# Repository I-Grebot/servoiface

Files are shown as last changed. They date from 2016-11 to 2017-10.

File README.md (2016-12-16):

# servoiface

DC Servo motor interface

Board use to control a DC motor and act as a servomotor, based on STM32F042 MCU. 

Position feedback can be provided by potentiometer, limit switches or encoder. 

Reference position command can be provided from a PWM signal such as regular RC servomotors, or an halfduplex UART such as Dynamixel smart servomotors.

Motor current limitation can be driven, thus the device can be used as a torque controlled system (useful for robot gripper, for instance).

Debug RGB, tactile switch, and potentiometer can be used for system calibration and visual feedback.

Board:

board

Schematics:

sch

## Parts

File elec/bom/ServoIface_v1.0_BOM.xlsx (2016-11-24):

Cmd | Qty | Value | Device | Package | Parts | Description
 | 3 |  | JUMPER-3SMD | SJ_3 | J_ES1, J_ES2, J_REF
 | 1 |  | JUMPER-PAD-2-NO | PAD-JUMPER-2-NO_NO_SILK | J_CMD
 | 1 |  | LNRG_4026 | NRG_4026 | L1
 | 2 |  | M03SCREW | SCREWTERMINAL-3.5MM-3 | POT, VIN1 | Header 3
 | 2 |  | M04SCREW | SCREWTERMINAL-3.5MM-4 | ENCODER, ENDSTOPS | Header 4
 | 5 |  | R0603 | R0603 | R3, R5, R7, R8, R9
 | 2 |  | SWITCH-MOMENTARY-2SMD-3 | TACTILE_SWITCH_SMD-3 | S1, S_RST | Various NO switches- pushbuttons, reed, etc
 | 1 | 47UF | C_PANAFM1E470-P2.0 | CAPPR200-500X1600 | C13 | Aluminum Electrolytic Capacitors
 | 1 | 0.15 | R2512 | CRF2512 | R1
 | 3 | 100nF | C0603 | R0603 | C1, C6, C10
 | 1 | 105k | R0603 | R0603 | R11
 | 1 | 10nF | C0603 | R0603 | C2
 | 2 | 10uF | C0805 | R0805 | C7, C8
 | 1 | 10uF | C1206 | 1206 | C9
 | 2 | 1uF | C0805 | R0805 | C3, C11
 | 1 | 2.2uF | C0805 | R0805 | C12
 | 1 | 20k | R0603 | R0603 | R12
 | 1 | 330k | R0603 | R0603 | R6
 | 3 | 4.7k | R0603 | R0603 | R2, R4, R10
 | 1 | 4.7uF | C0805 | R0805 | C4
 | 1 | 470nF | C0603 | R0603 | C5
 | 1 | DRV8870 | DRV8870 | HSOP_8P | IC4 | DRV8870 3.6-A Brushed DC Motor Driver (PWM Control)
 | 1 | HEAT_SINK | HEAT_SINK | HEAT_A5_SA | H1 | ICK SMD A 5 SA Farnell 4302163
 | 1 | J_SWD | ZIF-06-1MM | ZIF-06-1MM | J1
 | 1 | LED-TRICOLOR | LED-TRICOLOR | PLCC4 | RGB | Tri-Color LED SMD
 | 1 | LP2980 | LP2980 | SOT23-5L | IC3
 | 1 | M023.5MM | M023.5MM | SCREWTERMINAL-3.5MM-2 | MOTOR | Standard 2-pin 0.1 header. Use with"
 | 2 | NC | R0603 | R0603 | R13, R14
 | 1 | STM32F042 | STM32F042 | TSSOP20 | IC1 | ARM®-based 32-bit MCU, up to 32 KB Flash, crystal-less USB
 | 3 | TEST_POINT_R04 | TEST_POINT_R04 | TP_R04 | TP1, TP2, TP3
Ti | 1 | TPS560200 | TPS560200 | SOT23-5L | IC2
 | 1 | TRIMPOTCB10 | TRIMPOTCB10 | POT_CB10 | P1 | Various small potentiometers for set-and-forget" applications"

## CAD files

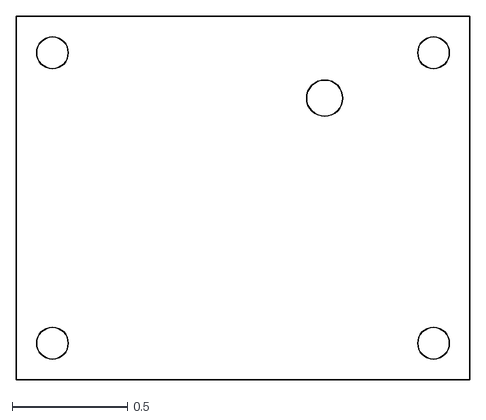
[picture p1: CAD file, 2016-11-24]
elec/dxf/ServoIface_v1.0.dxf
1.97 x 1.57

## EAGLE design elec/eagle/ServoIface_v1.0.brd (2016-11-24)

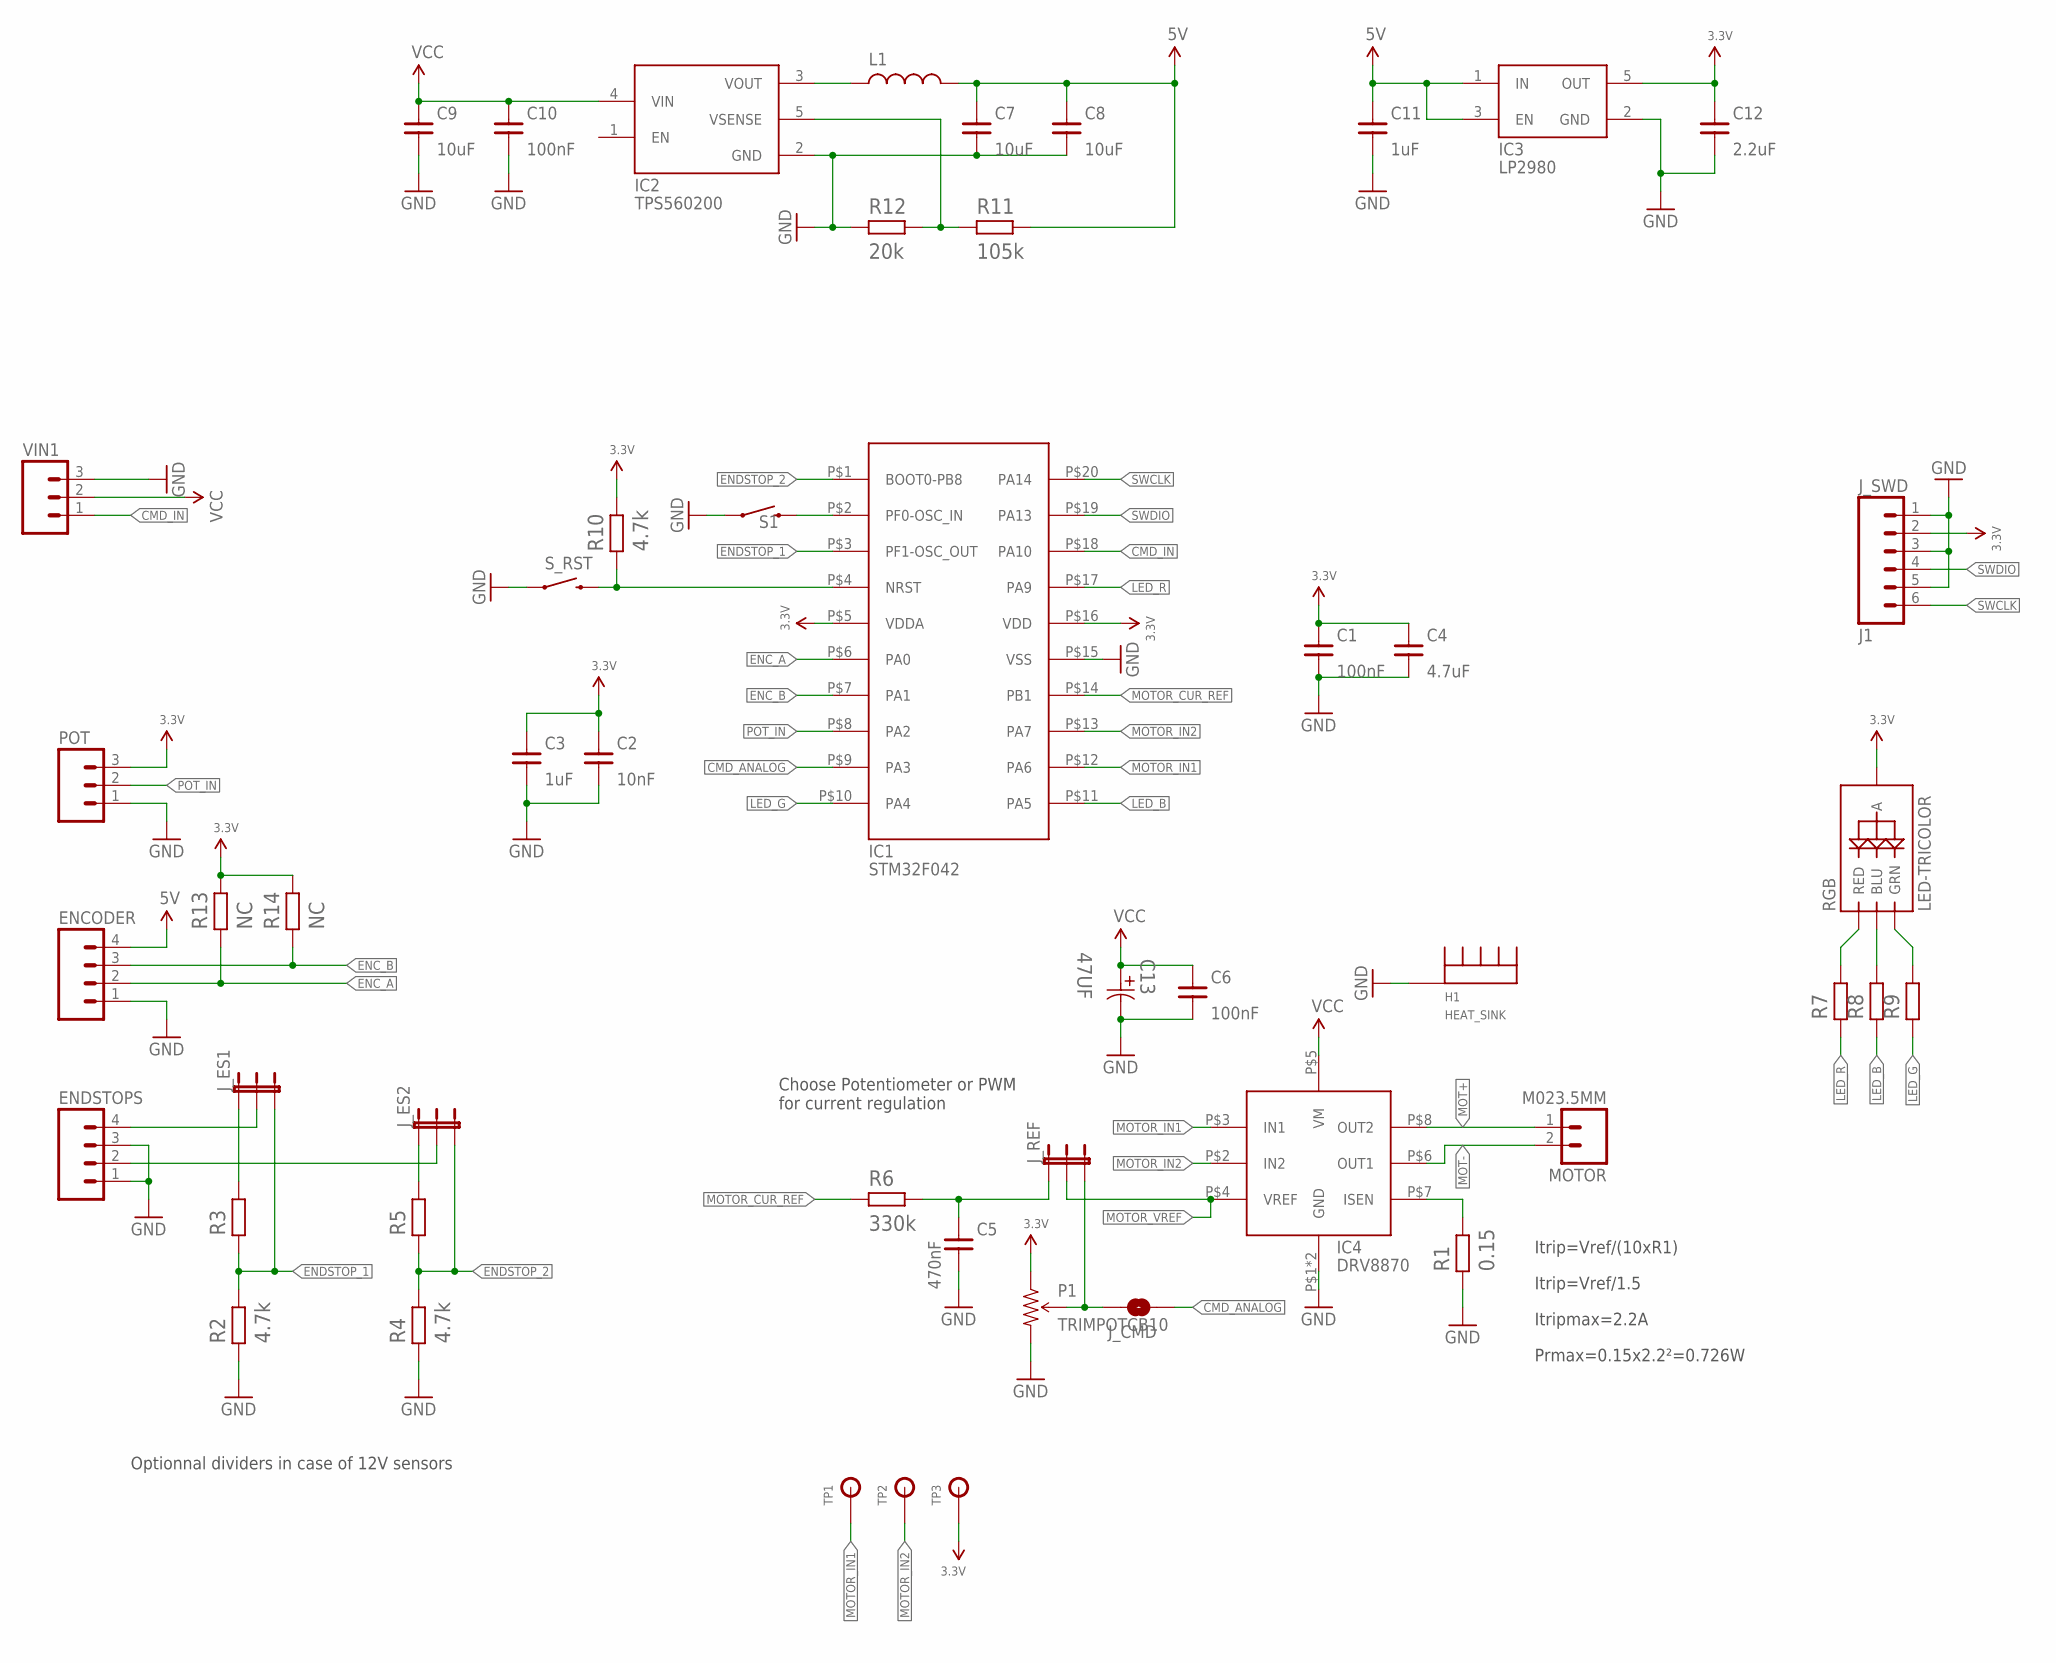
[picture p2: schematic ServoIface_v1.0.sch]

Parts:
C1, C6, C10: 100nF; R0603
C2: 10nF; R0603
C3, C11: 1uF; R0805
C4: 4.7uF; R0805
C5: 470nF; R0603
C7, C8: 10uF; R0805
C9: 10uF; 1206
C12: 2.2uF; R0805
C13: 47UF; CAPPR200-500X1600
ENCODER: M04SCREW; SCREWTERMINAL-3.5MM-4
ENDSTOPS: M04SCREW; SCREWTERMINAL-3.5MM-4
H1: HEAT_SINK; HEAT_A5_SA
IC1: STM32F042; TSSOP20
IC2: TPS560200; SOT23-5L
IC3: LP2980; SOT23-5L
IC4: DRV8870; HSOP_8P
J1: J_SWD; ZIF-06-1MM
J_CMD: JUMPER-PAD-2-NO; PAD-JUMPER-2-NO_NO_SILK
J_ES1, J_ES2: JUMPER-3SMD; SJ_3
J_REF: JUMPER-3SMD; SJ_3
L1: LNRG_4026; NRG_4026
MOTOR: M023.5MM; SCREWTERMINAL-3.5MM-2
P1: TRIMPOTCB10; POT_CB10
POT: M03SCREW; SCREWTERMINAL-3.5MM-3
R1: 0.15; CRF2512
R2, R4, R10: 4.7k; R0603
R3, R5, R7, R8, R9: R0603
R6: 330k; R0603
R11: 105k; R0603
R12: 20k; R0603
R13, R14: NC; R0603
RGB: LED-TRICOLOR; PLCC4
S1: SWITCH-MOMENTARY-2SMD-3; TACTILE_SWITCH_SMD-3
S_RST: SWITCH-MOMENTARY-2SMD-3; TACTILE_SWITCH_SMD-3
TP1, TP2, TP3: TEST_POINT_R04; TP_R04
VIN1: M03SCREW; SCREWTERMINAL-3.5MM-3

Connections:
3.3V: C1.2, C2.2, C3.2, C4.2, C12.2, IC1.P$5 (VDDA), IC1.P$16 (VDD), IC3.5 (OUT), J1.2, P1.P$1 (CCW), POT.3, R10.2, R13.2, R14.2, RGB.P$1 (A), TP3.P$1
5V: C7.2, C8.2, C11.2, ENCODER.4, IC3.1 (IN), IC3.3 (EN), L1.P$2 (2), R11.2
CMD_ANALOG: IC1.P$9 (PA3), J_CMD.1
CMD_IN: IC1.P$18 (PA10), VIN1.1
ENC_A: ENCODER.2, IC1.P$6 (PA0), R13.1
ENC_B: ENCODER.3, IC1.P$7 (PA1), R14.1
ENDSTOP_1: IC1.P$3 (PF1-OSC_OUT), J_ES1.3, R2.2, R3.1
ENDSTOP_2: IC1.P$1 (BOOT0-PB8), J_ES2.3, R4.2, R5.1
GND: C1.1, C2.1, C3.1, C4.1, C5.1, C6.1, C7.1, C8.1, C9.1, C10.1, C11.1, C12.1, C13.2, ENCODER.1, ENDSTOPS.1, ENDSTOPS.3, H1.P$1, IC1.P$15 (VSS), IC2.2 (GND), IC3.2 (GND), IC4.P$1 (GND), IC4.PAD (GND), J1.1, J1.3, J1.5, P1.P$2 (CW), POT.1, R1.P$1 (1), R2.1, R4.1, R12.1, S1.1, S_RST.1, VIN1.3
LED_B: IC1.P$11 (PA5), R8.1
LED_G: IC1.P$10 (PA4), R9.1
LED_R: IC1.P$17 (PA9), R7.1
MOT+: IC4.P$8 (OUT2), MOTOR.1
MOT-: IC4.P$6 (OUT1), MOTOR.2
MOTOR_CUR_REF: IC1.P$14 (PB1), R6.1
MOTOR_IN1: IC1.P$12 (PA6), IC4.P$3 (IN1), TP1.P$1
MOTOR_IN2: IC1.P$13 (PA7), IC4.P$2 (IN2), TP2.P$1
MOTOR_VREF: IC4.P$4 (VREF), J_REF.2
unnamed: IC4.P$7 (ISEN), R1.P$2 (2)
unnamed: ENDSTOPS.2, J_ES2.2
unnamed: J_ES2.1, R5.2
unnamed: ENDSTOPS.4, J_ES1.2
unnamed: J_ES1.1, R3.2
unnamed: J_CMD.2, J_REF.3, P1.P$3 (WIPER)
unnamed: C5.2, J_REF.1, R6.2
unnamed: R7.2, RGB.P$4 (RED)
unnamed: R8.2, RGB.P$2 (BLU)
unnamed: R9.2, RGB.P$3 (GRN)
unnamed: IC1.P$4 (NRST), R10.1, S_RST.4 (2)
unnamed: IC2.3 (VOUT), L1.P$1 (1)
unnamed: IC2.5 (VSENSE), R11.1, R12.2
POT_IN: IC1.P$8 (PA2), POT.2
SW1: IC1.P$2 (PF0-OSC_IN), S1.4 (2)
SWCLK: IC1.P$20 (PA14), J1.6
SWDIO: IC1.P$19 (PA13), J1.4
VCC: C6.2, C9.2, C10.2, C13.1, IC2.4 (VIN), IC4.P$5 (VM), VIN1.2

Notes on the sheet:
Itrip=Vref/(10xR1)
Itrip=Vref/1.5
Itripmax=2.2A
Optionnal dividers in case of 12V sensors
Choose Potentiometer or PWM for current regulation
Prmax=0.15x2.2²=0.726W

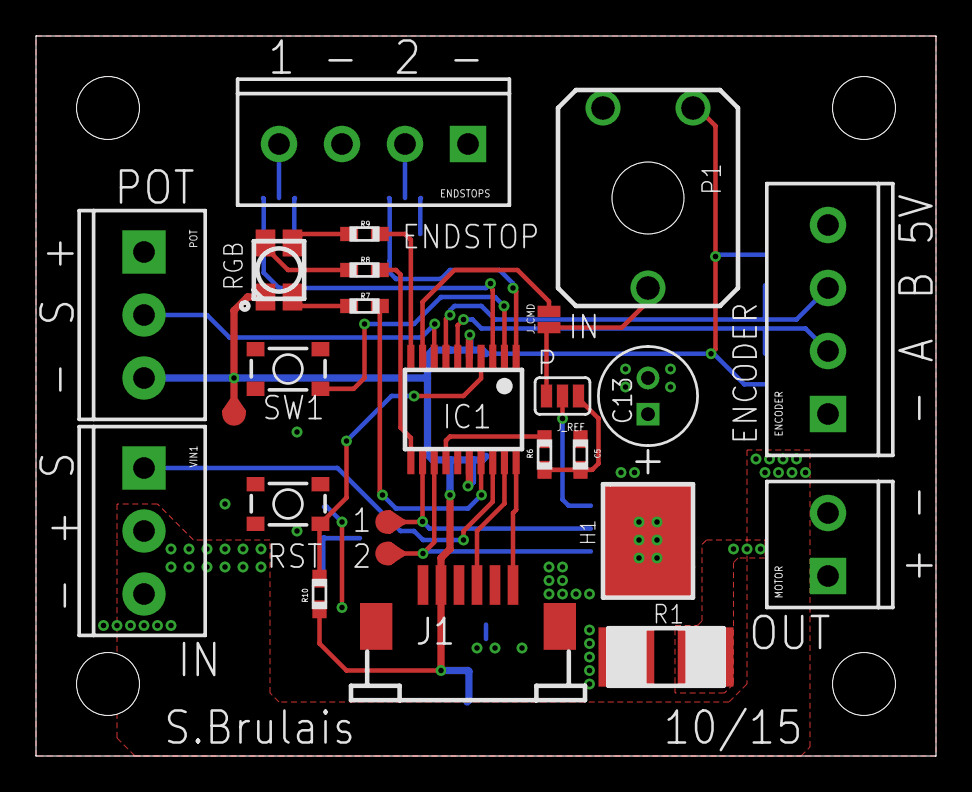
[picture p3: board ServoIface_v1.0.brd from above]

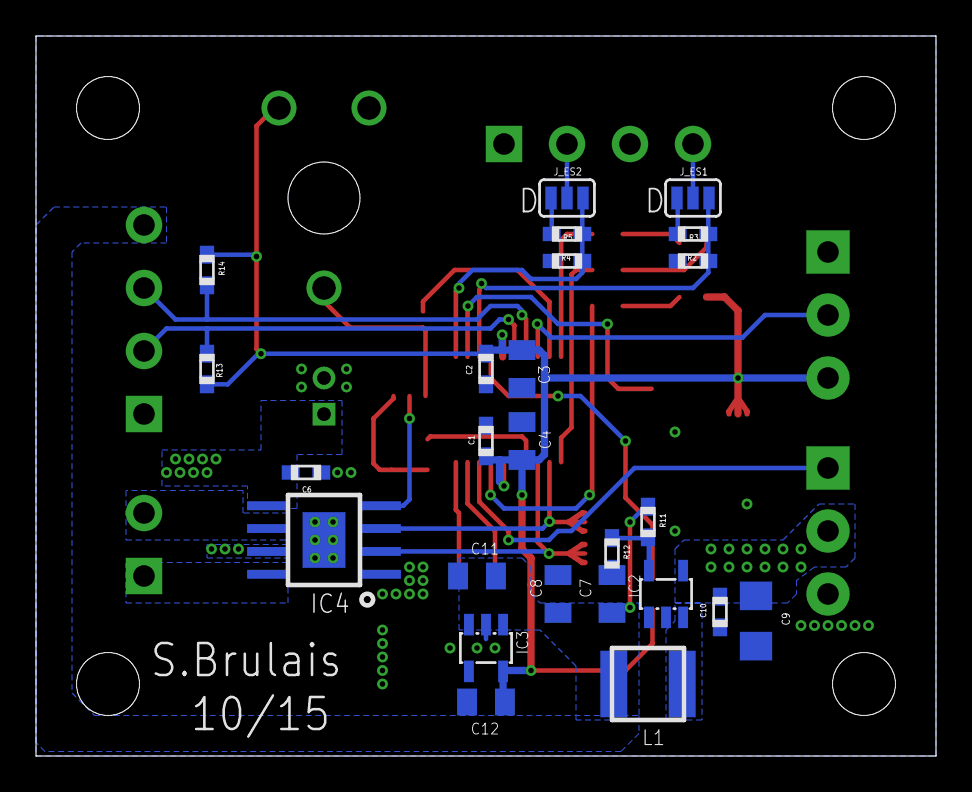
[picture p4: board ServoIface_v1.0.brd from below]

Board: 2 copper layers, 50.0 x 40.0 mm, 50 parts (25 on the bottom side), 36 nets.

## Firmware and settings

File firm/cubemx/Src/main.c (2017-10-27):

/**
  ******************************************************************************
  * File Name          : main.c
  * Description        : Main program body
  ******************************************************************************
  *
  * Copyright (c) 2017 STMicroelectronics International N.V. 
  * All rights reserved.
  *
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
  ******************************************************************************
  */
/* Includes ------------------------------------------------------------------*/
#include "main.h"
#include "stm32f0xx_hal.h"
#include "cmsis_os.h"



/* USER CODE BEGIN Includes */
#include "ServoIface.h"
#include "pid.h"

/* USER CODE END Includes */

ADC_HandleTypeDef hadc;
DMA_HandleTypeDef hdma_adc;

TIM_HandleTypeDef htim1;
TIM_HandleTypeDef htim2;
TIM_HandleTypeDef htim3;

osThreadId MotorCtrlTaskIdHandle;
osThreadId RGBLedTaskIdHandle;
osThreadId AutoTestTaskIdHandle;
osSemaphoreId selfTestSemHandle;

/* USER CODE BEGIN PV */
PID_process_t *pPID;
volatile uint32_t pwm=0;


/* USER CODE END PV */

void SystemClock_Config(void);
void Error_Handler(void);
static void MX_GPIO_Init(void);
static void MX_DMA_Init(void);
static void MX_ADC_Init(void);
static void MX_TIM1_Init(void);
static void MX_TIM2_Init(void);
static void MX_TIM3_Init(void);
void MotorCtrlTask(void const * argument);
void RGBLedTask(void const * argument);
void PIDTask(void const * argument);

void HAL_TIM_MspPostInit(TIM_HandleTypeDef *htim);
                                

/* USER CODE BEGIN PFP */

/* USER CODE END PFP */

int main(void)
{

  /* MCU Configuration----------------------------------------------------------*/

  /* Reset of all peripherals, Initializes the Flash interface and the Systick. */
  HAL_Init();

  /* Configure the system clock */
  SystemClock_Config();

  /* Initialize all configured peripherals */
  MX_GPIO_Init();
  MX_DMA_Init();
  MX_ADC_Init();
  MX_TIM1_Init();
  MX_TIM2_Init();
  MX_TIM3_Init();

  /* USER CODE BEGIN 2 */


  HAL_TIM_PWM_Start(&htim3, TIM_CHANNEL_1);
  HAL_TIM_PWM_Start(&htim3, TIM_CHANNEL_2);
  HAL_TIM_Encoder_Start(&htim2,TIM_CHANNEL_1|TIM_CHANNEL_2);
  HAL_TIM_IC_Start_IT(&htim1, TIM_CHANNEL_3);

  /*Init PID library*/
  pPID = pid_init(); //position PID
  PID_Set_Coefficient(pPID->PID,50,1,260,0); // KP, KI, KD, Ilimit
  PID_Set_limitation(pPID,1024,0);

  /* USER CODE END 2 */

  /* USER CODE BEGIN RTOS_MUTEX */
  /* add mutexes, ... */
  /* USER CODE END RTOS_MUTEX */

  /* Create the semaphores(s) */
  /* definition and creation of selfTestSem */
  osSemaphoreDef(selfTestSem);
  selfTestSemHandle = osSemaphoreCreate(osSemaphore(selfTestSem), 1);

  /* USER CODE BEGIN RTOS_SEMAPHORES */
  /* add semaphores, ... */
  /* USER CODE END RTOS_SEMAPHORES */

  /* USER CODE BEGIN RTOS_TIMERS */
  /* start timers, add new ones, ... */
  /* USER CODE END RTOS_TIMERS */

  /* Create the thread(s) */
  /* definition and creation of MotorCtrlTaskId */
  osThreadDef(MotorCtrlTaskId, MotorCtrlTask, osPriorityNormal, 0, 128);
  MotorCtrlTaskIdHandle = osThreadCreate(osThread(MotorCtrlTaskId), NULL);

  /* definition and creation of RGBLedTaskId */
  osThreadDef(RGBLedTaskId, RGBLedTask, osPriorityNormal, 0, 128);
  RGBLedTaskIdHandle = osThreadCreate(osThread(RGBLedTaskId), NULL);

  /* definition and creation of AutoTestTaskId */
  osThreadDef(AutoTestTaskId, PIDTask, osPriorityIdle, 0, 128);
  AutoTestTaskIdHandle = osThreadCreate(osThread(AutoTestTaskId), NULL);

  /* USER CODE BEGIN RTOS_THREADS */
  /* add threads, ... */
  /* USER CODE END RTOS_THREADS */

  /* USER CODE BEGIN RTOS_QUEUES */
  /* add queues, ... */
  /* USER CODE END RTOS_QUEUES */
 

  /* Start scheduler */
  osKernelStart();
  
  /* We should never get here as control is now taken by the scheduler */

  /* Infinite loop */
  /* USER CODE BEGIN WHILE */
  while (1)
  {
  /* USER CODE END WHILE */

  /* USER CODE BEGIN 3 */

  }
  /* USER CODE END 3 */

}

/** System Clock Configuration
*/
void SystemClock_Config(void)
{

  RCC_OscInitTypeDef RCC_OscInitStruct;
  RCC_ClkInitTypeDef RCC_ClkInitStruct;

    /**Initializes the CPU, AHB and APB busses clocks 
    */
  RCC_OscInitStruct.OscillatorType = RCC_OSCILLATORTYPE_HSI48;
  RCC_OscInitStruct.HSI48State = RCC_HSI48_ON;
  RCC_OscInitStruct.PLL.PLLState = RCC_PLL_NONE;
  if (HAL_RCC_OscConfig(&RCC_OscInitStruct) != HAL_OK)
  {
    Error_Handler();
  }

    /**Initializes the CPU, AHB and APB busses clocks 
    */
  RCC_ClkInitStruct.ClockType = RCC_CLOCKTYPE_HCLK|RCC_CLOCKTYPE_SYSCLK
                              |RCC_CLOCKTYPE_PCLK1;
  RCC_ClkInitStruct.SYSCLKSource = RCC_SYSCLKSOURCE_HSI48;
  RCC_ClkInitStruct.AHBCLKDivider = RCC_SYSCLK_DIV1;
  RCC_ClkInitStruct.APB1CLKDivider = RCC_HCLK_DIV1;

  if (HAL_RCC_ClockConfig(&RCC_ClkInitStruct, FLASH_LATENCY_1) != HAL_OK)
  {
    Error_Handler();
  }

    /**Configure the Systick interrupt time 
    */
  HAL_SYSTICK_Config(HAL_RCC_GetHCLKFreq()/1000);

    /**Configure the Systick 
    */
  HAL_SYSTICK_CLKSourceConfig(SYSTICK_CLKSOURCE_HCLK);

  /* SysTick_IRQn interrupt configuration */
  HAL_NVIC_SetPriority(SysTick_IRQn, 3, 0);
}

/* ADC init function */
static void MX_ADC_Init(void)
{

  ADC_ChannelConfTypeDef sConfig;

    /**Configure the global features of the ADC (Clock, Resolution, Data Alignment and number of conversion) 
    */
  hadc.Instance = ADC1;
  hadc.Init.ClockPrescaler = ADC_CLOCK_SYNC_PCLK_DIV4;
  hadc.Init.Resolution = ADC_RESOLUTION_12B;
  hadc.Init.DataAlign = ADC_DATAALIGN_RIGHT;
  hadc.Init.ScanConvMode = ADC_SCAN_DIRECTION_FORWARD;
  hadc.Init.EOCSelection = ADC_EOC_SINGLE_CONV;
  hadc.Init.LowPowerAutoWait = DISABLE;
  hadc.Init.LowPowerAutoPowerOff = DISABLE;
  hadc.Init.ContinuousConvMode = ENABLE;
  hadc.Init.DiscontinuousConvMode = DISABLE;
  hadc.Init.ExternalTrigConv = ADC_SOFTWARE_START;
  hadc.Init.ExternalTrigConvEdge = ADC_EXTERNALTRIGCONVEDGE_NONE;
  hadc.Init.DMAContinuousRequests = ENABLE;
  hadc.Init.Overrun = ADC_OVR_DATA_PRESERVED;
  if (HAL_ADC_Init(&hadc) != HAL_OK)
  {
    Error_Handler();
  }

    /**Configure for the selected ADC regular channel to be converted. 
    */
  sConfig.Channel = ADC_CHANNEL_2;
  sConfig.Rank = ADC_RANK_CHANNEL_NUMBER;
  sConfig.SamplingTime = ADC_SAMPLETIME_1CYCLE_5;
  if (HAL_ADC_ConfigChannel(&hadc, &sConfig) != HAL_OK)
  {
    Error_Handler();
  }

    /**Configure for the selected ADC regular channel to be converted. 
    */
  sConfig.Channel = ADC_CHANNEL_3;
  if (HAL_ADC_ConfigChannel(&hadc, &sConfig) != HAL_OK)
  {
    Error_Handler();
  }

}

/* TIM1 init function */
static void MX_TIM1_Init(void)
{

  TIM_ClockConfigTypeDef sClockSourceConfig;
  TIM_MasterConfigTypeDef sMasterConfig;
  TIM_IC_InitTypeDef sConfigIC;

  htim1.Instance = TIM1;
  htim1.Init.Prescaler = 0;
  htim1.Init.CounterMode = TIM_COUNTERMODE_UP;
  htim1.Init.Period = 65535;
  htim1.Init.ClockDivision = TIM_CLOCKDIVISION_DIV1;
  htim1.Init.RepetitionCounter = 0;
  htim1.Init.AutoReloadPreload = TIM_AUTORELOAD_PRELOAD_DISABLE;
  if (HAL_TIM_Base_Init(&htim1) != HAL_OK)
  {
    Error_Handler();
  }

  sClockSourceConfig.ClockSource = TIM_CLOCKSOURCE_INTERNAL;
  if (HAL_TIM_ConfigClockSource(&htim1, &sClockSourceConfig) != HAL_OK)
  {
    Error_Handler();
  }

  if (HAL_TIM_IC_Init(&htim1) != HAL_OK)
  {
    Error_Handler();
  }

  sMasterConfig.MasterOutputTrigger = TIM_TRGO_RESET;
  sMasterConfig.MasterSlaveMode = TIM_MASTERSLAVEMODE_DISABLE;
  if (HAL_TIMEx_MasterConfigSynchronization(&htim1, &sMasterConfig) != HAL_OK)
  {
    Error_Handler();
  }

  sConfigIC.ICPolarity = TIM_INPUTCHANNELPOLARITY_BOTHEDGE;
  sConfigIC.ICSelection = TIM_ICSELECTION_DIRECTTI;
  sConfigIC.ICPrescaler = TIM_ICPSC_DIV1;
  sConfigIC.ICFilter = 0;
  if (HAL_TIM_IC_ConfigChannel(&htim1, &sConfigIC, TIM_CHANNEL_3) != HAL_OK)
  {
    Error_Handler();
  }

}

/* TIM2 init function */
static void MX_TIM2_Init(void)
{

  TIM_Encoder_InitTypeDef sConfig;
  TIM_MasterConfigTypeDef sMasterConfig;

  htim2.Instance = TIM2;
  htim2.Init.Prescaler = 0;
  htim2.Init.CounterMode = TIM_COUNTERMODE_UP;
  htim2.Init.Period = 0xFFFFFFFF;//0;
  htim2.Init.ClockDivision = TIM_CLOCKDIVISION_DIV1;
  htim2.Init.AutoReloadPreload = TIM_AUTORELOAD_PRELOAD_DISABLE;
  sConfig.EncoderMode = TIM_ENCODERMODE_TI12;
  sConfig.IC1Polarity = TIM_ICPOLARITY_RISING;
  sConfig.IC1Selection = TIM_ICSELECTION_DIRECTTI;
  sConfig.IC1Prescaler = TIM_ICPSC_DIV1;
  sConfig.IC1Filter = 0;
  sConfig.IC2Polarity = TIM_ICPOLARITY_RISING;
  sConfig.IC2Selection = TIM_ICSELECTION_DIRECTTI;
  sConfig.IC2Prescaler = TIM_ICPSC_DIV1;
  sConfig.IC2Filter = 0;
  if (HAL_TIM_Encoder_Init(&htim2, &sConfig) != HAL_OK)
  {
    Error_Handler();
  }

  sMasterConfig.MasterOutputTrigger = TIM_TRGO_RESET;
  sMasterConfig.MasterSlaveMode = TIM_MASTERSLAVEMODE_DISABLE;
  if (HAL_TIMEx_MasterConfigSynchronization(&htim2, &sMasterConfig) != HAL_OK)
  {
    Error_Handler();
  }

}

/* TIM3 init function */
static void MX_TIM3_Init(void)
{

  TIM_MasterConfigTypeDef sMasterConfig;
  TIM_OC_InitTypeDef sConfigOC;

  htim3.Instance = TIM3;
  htim3.Init.Prescaler = (uint16_t) (SystemCoreClock / 21000000) - 1;//0;
  htim3.Init.CounterMode = TIM_COUNTERMODE_UP;
  htim3.Init.Period = MOTOR_PWM_PERIOD;
  htim3.Init.ClockDivision = TIM_CLOCKDIVISION_DIV1;
  htim3.Init.AutoReloadPreload = TIM_AUTORELOAD_PRELOAD_DISABLE;
  if (HAL_TIM_PWM_Init(&htim3) != HAL_OK)
  {
    Error_Handler();
  }

  sMasterConfig.MasterOutputTrigger = TIM_TRGO_RESET;
  sMasterConfig.MasterSlaveMode = TIM_MASTERSLAVEMODE_DISABLE;
  if (HAL_TIMEx_MasterConfigSynchronization(&htim3, &sMasterConfig) != HAL_OK)
  {
    Error_Handler();
  }

  sConfigOC.OCMode = TIM_OCMODE_PWM1;
  sConfigOC.Pulse = MOTOR_PWM_PERIOD / 2; // 50%
  sConfigOC.OCPolarity = TIM_OCPOLARITY_HIGH;
  sConfigOC.OCFastMode = TIM_OCFAST_DISABLE;
  if (HAL_TIM_PWM_ConfigChannel(&htim3, &sConfigOC, TIM_CHANNEL_1) != HAL_OK)
  {
    Error_Handler();
  }

  if (HAL_TIM_PWM_ConfigChannel(&htim3, &sConfigOC, TIM_CHANNEL_2) != HAL_OK)
  {
    Error_Handler();
  }

  if (HAL_TIM_PWM_ConfigChannel(&htim3, &sConfigOC, TIM_CHANNEL_4) != HAL_OK)
  {
    Error_Handler();
  }

  HAL_TIM_MspPostInit(&htim3);

}

/** 
  * Enable DMA controller clock
  */
static void MX_DMA_Init(void) 
{
  /* DMA controller clock enable */
  __HAL_RCC_DMA1_CLK_ENABLE();

  /* DMA interrupt init */
  /* DMA1_Channel1_IRQn interrupt configuration */
  HAL_NVIC_SetPriority(DMA1_Channel1_IRQn, 3, 0);
  HAL_NVIC_EnableIRQ(DMA1_Channel1_IRQn);

}

/** Configure pins as 
        * Analog 
        * Input 
        * Output
        * EVENT_OUT
        * EXTI
*/
static void MX_GPIO_Init(void)
{

  GPIO_InitTypeDef GPIO_InitStruct;

  /* GPIO Ports Clock Enable */
  __HAL_RCC_GPIOA_CLK_ENABLE();
  __HAL_RCC_GPIOB_CLK_ENABLE();
  __HAL_RCC_GPIOF_CLK_ENABLE();

  /*Configure GPIO pin Output Level */
  HAL_GPIO_WritePin(GPIOA, LED_G_Pin|LED_B_Pin|LED_R_Pin, GPIO_PIN_RESET);

  /*Configure GPIO pin : ENDSTOP_2_Pin */
  GPIO_InitStruct.Pin = ENDSTOP_2_Pin;
  GPIO_InitStruct.Mode = GPIO_MODE_INPUT; // GPIO_MODE_IT_RISING;
  GPIO_InitStruct.Pull = GPIO_NOPULL;
  HAL_GPIO_Init(ENDSTOP_2_GPIO_Port, &GPIO_InitStruct);

  /*Configure GPIO pin : CMD_IN_Pin */
  GPIO_InitStruct.Pin = CMD_IN_Pin;
  GPIO_InitStruct.Mode = GPIO_MODE_INPUT;
  GPIO_InitStruct.Pull = GPIO_PULLDOWN;
  HAL_GPIO_Init(CMD_IN_GPIO_Port, &GPIO_InitStruct);

  /*Configure GPIO pin : SW1_Pin */
  GPIO_InitStruct.Pin = SW1_Pin;
  GPIO_InitStruct.Mode = GPIO_MODE_IT_FALLING;
  GPIO_InitStruct.Pull = GPIO_PULLUP;
  HAL_GPIO_Init(SW1_GPIO_Port, &GPIO_InitStruct);

  /*Configure GPIO pin : ENDSTOP_1_Pin */
  GPIO_InitStruct.Pin = ENDSTOP_1_Pin;
  GPIO_InitStruct.Mode = GPIO_MODE_IT_RISING_FALLING;
  GPIO_InitStruct.Pull = GPIO_PULLUP;
  HAL_GPIO_Init(ENDSTOP_1_GPIO_Port, &GPIO_InitStruct);

  /*Configure GPIO pins : LED_G_Pin LED_B_Pin LED_R_Pin */
  GPIO_InitStruct.Pin = LED_G_Pin|LED_B_Pin|LED_R_Pin;
  GPIO_InitStruct.Mode = GPIO_MODE_OUTPUT_PP;
  GPIO_InitStruct.Pull = GPIO_NOPULL;
  GPIO_InitStruct.Speed = GPIO_SPEED_FREQ_LOW;
  HAL_GPIO_Init(GPIOA, &GPIO_InitStruct);

  /* EXTI interrupt init*/
  HAL_NVIC_SetPriority(EXTI0_1_IRQn, 3, 0);
  HAL_NVIC_EnableIRQ(EXTI0_1_IRQn);

}

/* USER CODE BEGIN 4 */
/**
  * @brief Hardware function for setting the motor speed.
  * @param speed: the new motor speed. If positive the motor will move forward, if negative it will move backward.
  */
void HwSetMotorSpeed(int speed) {
	/*Check if PWM is out of range*/
	if(speed > MOTOR_PWM_PERIOD)
	{
		speed = MOTOR_PWM_PERIOD;
	}else if(speed < (-MOTOR_PWM_PERIOD) )
	{
		speed = -MOTOR_PWM_PERIOD;
	}

	/*Apply PWM upon speed sign*/
	if(speed > 0) {
		TIM3->CCR1 = 0;
		TIM3->CCR2 = speed;
	} else if (speed < 0) {
		TIM3->CCR1 = speed * -1;
		TIM3->CCR2 = 0;
	} else {
		TIM3->CCR1 = 0;
		TIM3->CCR2 = 0;
	}
}

/**
  * @brief Hardware function for getting the current motor position. Unit = ticks as read by the encoder.
  */
int32_t HwGetCurrentPosition() {
	int32_t output = 0;

	output = TIM2->CNT;

	return output;
}

uint8_t HwGetCommand(void)
{
  return (((HAL_GPIO_ReadPin(CMD_IN_GPIO_Port,    CMD_IN_Pin)    == GPIO_PIN_SET?1:0) << 1U) |
          ((HAL_GPIO_ReadPin(ENDSTOP_2_GPIO_Port, ENDSTOP_2_Pin) == GPIO_PIN_SET?1:0) << 0U));
}

/**
  * @brief Hardware function called when the goal is reached.
  */
void HwGoalIsReached() {
	//TODO: code for SPI feedback when goal is reached

}

/**
  * @brief Hardware function called when the goal is set.
  */
void HwGoalIsActive() {
	//TODO: code for SPI feedback when goal is set

}
/* USER CODE END 4 */

/* MotorCtrlTask function */
void MotorCtrlTask(void const * argument)
{
  /* USER CODE BEGIN 5 */

  uint8_t command ;
  uint8_t prev_command;
  bool initialized = false; // prevent over-run if not init

	set_hw_set_motor_speed(HwSetMotorSpeed);
	set_hw_get_current_position(HwGetCurrentPosition);
	set_hw_goal_is_active(HwGoalIsActive);
	set_hw_goal_is_reached(HwGoalIsReached);

	command = CMD_NOP;
	prev_command = CMD_NOP;


  for(;;)
  {
	  LED_YELLOW;
	  osDelay(1000);
	  PID_Set_limitation(pPID,1024,0);
	  TIM2->CNT=0;
	  PID_Set_Ref_Position(pPID,8000);
	  LED_MAGENTA;
	  osDelay(2000);
	  PID_Set_limitation(pPID,150,0);
	  PID_Set_Ref_Position(pPID,0);
	  LED_BLUE;
	  osDelay(2000);
  }
  /* Infinite loop */
  for(;;)
  {

    command = HwGetCommand();

    // Take action only on command changes
    if(prev_command != command)
    {
      switch(command)
      {

        // Goto Left + Init
        case CMD_GOTO_LEFT:
          LED_YELLOW;
          CheckForZero();
          while(ZeroIsFound() == 0); // wait for endstop trigger
          initialized = true;
          LED_GREEN;
          break;

        case CMD_GOTO_MIDDLE:
          if(initialized)
          {
            LED_CYAN;
            SetObjective(POS_MIDDLE);
            GoToObjective();
            LED_GREEN;
          }

          break;

        case CMD_GOTO_RIGHT:
          if(initialized)
          {
            LED_MAGENTA;
            SetObjective(POS_RIGHT);
            GoToObjective();
            LED_GREEN;
          }
          break;

        default:
          case CMD_NOP:
            LED_BLUE;
            break;
      }
    } // if (command change)

    prev_command = command;

    // Delay in ms
    osDelay(10);

  }

  /* USER CODE END 5 */ 
}

/* RGBLedTask function */
void RGBLedTask(void const * argument)
{
  GPIO_PinState LED_R_Pin_state;
  GPIO_PinState LED_G_Pin_state;
  GPIO_PinState LED_B_Pin_state;
  /* USER CODE BEGIN RGBLedTask */
  /* Infinite loop */
  /*Just toggle LEDs*/
  for(;;)
  {
	/*Save LEDs state*/
	LED_R_Pin_state = HAL_GPIO_ReadPin(GPIOA,LED_R_Pin);
	LED_G_Pin_state = HAL_GPIO_ReadPin(GPIOA,LED_G_Pin);
	LED_B_Pin_state = HAL_GPIO_ReadPin(GPIOA,LED_B_Pin);
	/*Shutdown all LEDs*/
	LED_OFF;
    osDelay(200);
    if(LED_R_Pin_state==0)
	{
    	HAL_GPIO_TogglePin(GPIOA,LED_R_Pin);
	}
    if(LED_G_Pin_state==0)
	{
    	HAL_GPIO_TogglePin(GPIOA,LED_G_Pin);
	}
    if(LED_B_Pin_state==0)
	{
    	HAL_GPIO_TogglePin(GPIOA,LED_B_Pin);
	}

    pwm = __HAL_TIM_GET_COMPARE(&htim1, TIM_CHANNEL_3);//XXX
  }
  /* USER CODE END RGBLedTask */
}

/* PIDTask function */
void PIDTask(void const * argument)
{
	uint32_t PreviousWakeTime = osKernelSysTick();
	int32_t i32CurPos=0;
	/* USER CODE BEGIN PIDTask */
	/* Infinite loop */
	for(;;)
	{
		/*Ensure constant time base*/
		osDelayUntil(&PreviousWakeTime,10);
		i32CurPos = GetCurrentPosition();
		PID_Process_Position(pPID, NULL, i32CurPos);

	}
	/* USER CODE END PIDTask */
}

/**
  * @brief  Period elapsed callback in non blocking mode
  * @note   This function is called  when TIM14 interrupt took place, inside
  * HAL_TIM_IRQHandler(). It makes a direct call to HAL_IncTick() to increment
  * a global variable "uwTick" used as application time base.
  * @param  htim : TIM handle
  * @retval None
  */
void HAL_TIM_PeriodElapsedCallback(TIM_HandleTypeDef *htim)
{
  if (htim->Instance == TIM14) {
    HAL_IncTick();
  }
}

void HAL_GPIO_EXTI_Callback(uint16_t GPIO_Pin)
{
	/* NOTE: This function should not be modified, when the callback is needed,
	  the HAL_GPIO_EXTI_Callback could be implemented in the user file
	*/
	if(ENDSTOP_1_Pin == GPIO_Pin) {
		if(HAL_GPIO_ReadPin(ENDSTOP_1_GPIO_Port, ENDSTOP_1_Pin) == 0) {
			ZeroTriggered();
		}
	}
}

/**
  * @brief  This function is executed in case of error occurrence.
  * @param  None
  * @retval None
  */
void Error_Handler(void)
{
  /* USER CODE BEGIN Error_Handler */
  /* User can add his own implementation to report the HAL error return state */
  while(1) 
  {
    LED_RED;
  }
  /* USER CODE END Error_Handler */ 
}

#ifdef USE_FULL_ASSERT

/**
   * @brief Reports the name of the source file and the source line number
   * where the assert_param error has occurred.
   * @param file: pointer to the source file name
   * @param line: assert_param error line source number
   * @retval None
   */
void assert_failed(uint8_t* file, uint32_t line)
{
  /* USER CODE BEGIN 6 */
  /* User can add his own implementation to report the file name and line number,
    ex: printf("Wrong parameters value: file %s on line %d\r\n", file, line) */
  /* USER CODE END 6 */

}

#endif

/**
  * @}
  */ 

/**
  * @}
*/ 

/************************ (C) COPYRIGHT STMicroelectronics *****END OF FILE****/

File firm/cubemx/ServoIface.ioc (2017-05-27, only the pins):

Mcu.UserName=STM32F042F6Px
PA0.GPIO_Label=ENC_A
PA0.Signal=S_TIM2_CH1_ETR
PA1.GPIO_Label=ENC_B
PA1.Signal=S_TIM2_CH2
PA10.GPIO_Label=CMD_IN
PA10.Signal=S_TIM1_CH3
PA13.Signal=SYS_SWDIO
PA14.Signal=SYS_SWCLK
PA2.GPIO_Label=POT_IN
PA2.Signal=ADC_IN2
PA3.GPIO_Label=CMD_ANALOG
PA3.Signal=ADC_IN3
PA4.GPIO_Label=LED_G
PA4.Signal=GPIO_Output
PA5.GPIO_Label=LED_B
PA5.Signal=GPIO_Output
PA6.GPIO_Label=MOT_IN1
PA6.Signal=S_TIM3_CH1
PA7.GPIO_Label=MOT_IN2
PA7.Signal=S_TIM3_CH2
PA9.GPIO_Label=LED_R
PA9.Signal=GPIO_Output
PB1.GPIO_Label=MOT_CUR
PB1.Signal=S_TIM3_CH4
PB8.GPIO_Label=ENDSTOP_2
PB8.Signal=GPXTI8
PF0-OSC_IN.GPIO_Label=SW1
PF0-OSC_IN.Signal=GPXTI0
PF1-OSC_OUT.GPIO_Label=ENDSTOP_1
PF1-OSC_OUT.Signal=GPXTI1

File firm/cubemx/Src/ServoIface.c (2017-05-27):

#include "main.h"
#include "stdint.h"
#include "stm32f0xx_hal.h"

int32_t encoder_0_value=0; // the tick number corresponding to slider's minimum limit
int32_t current_position = 0; // the tick number corresponding to the motor current position

int32_t goal_position; // the tick number that must be reached by the motor
int goal_is_active = 0; // 0 when no goal is set, 1 otherwise
int goal_is_forward = 0; // goal is forward when that encoder value should increase to get closer to the goal

int zero_is_found = 0; // 1 if the correct value for encoder_0_value has been set

// -----------------------------------------------------------------------------
// HARDWARE FUNCTION POINTERS
// -----------------------------------------------------------------------------
void (* hw_set_motor_speed)(int) = NULL;
int32_t (* hw_get_current_position)() = NULL;
void (* hw_goal_is_active)() = NULL;
void (* hw_goal_is_reached)() = NULL;


// -----------------------------------------------------------------------------
// HARDWARE FUNCTION INITIALIZERS
// -----------------------------------------------------------------------------
void set_hw_set_motor_speed(void (*hw_set_motor_speed_pointer)(int))
{
  hw_set_motor_speed = hw_set_motor_speed_pointer;
}

int32_t set_hw_get_current_position(int32_t (*hw_get_current_position_pointer)())
{
  hw_get_current_position = hw_get_current_position_pointer;
}

void set_hw_goal_is_active(void (*hw_goal_is_active_pointer)())
{
  hw_goal_is_active = hw_goal_is_active_pointer;
}

void set_hw_goal_is_reached(void (*hw_goal_is_reached_pointer)())
{
  hw_goal_is_reached = hw_goal_is_reached_pointer;
}


// -----------------------------------------------------------------------------
// HARDWARE FUNCTION BRIDGES
// -----------------------------------------------------------------------------

/**
  * @brief Set the motor speed.
  * @param speed: the new motor speed. If positive the motor will move forward, if negative it will move backward.
  */
void SetMotorSpeed(int speed) {
	hw_set_motor_speed(speed);
}

/**
  * @brief Called when the goal is reached.
  */
void GoalIsReached() {
	hw_goal_is_reached();
}

/**
  * @brief Called when the goal is set.
  */
void GoalIsActive() {
	hw_goal_is_active();
}

/**
  * @brief Return the current motor position. Unit = ticks as read by the encoder.
  */
int32_t GetCurrentPosition() {
	return hw_get_current_position();
}


// -----------------------------------------------------------------------------
// SERVOIFACE LOGIC
// -----------------------------------------------------------------------------

/**
  * @brief Set the new position to be reached.
  * @param goal_position_in_ticks: the new position to be reached. Unit = ticks as read by the encoder (min = 0, max = number of ticks to reach the end of the slider).
  */
void SetObjective (int32_t goal_position_in_ticks)
{
	int32_t goal_position_normalized = encoder_0_value + goal_position_in_ticks;

	if(goal_position_normalized != current_position) {

		if(goal_position_normalized > current_position) {
			goal_is_forward = 1;
		} else {
			goal_is_forward = 0;
		}
	}

	goal_position = goal_position_normalized;
	goal_is_active = 1;
	GoalIsActive();
}

/**
  * @brief Return 1 if the goal is reached, or 0 if not.
  */
int IsGoalReached() {
	int is_goal_reached = 0;

	current_position = GetCurrentPosition();

	if(goal_is_active == 0) {
		is_goal_reached = 1;
	} else {
		if((goal_is_forward == 1 && current_position >= goal_position)
		|| (goal_is_forward == 0 && current_position <= goal_position)) {
			is_goal_reached = 1;
		}
	}

	return is_goal_reached;
}

/**
  * @brief Move the motor to the objective. Must be called after SetObjective()
  */
void GoToObjective() {

	if(goal_is_forward == 1) {
		SetMotorSpeed(600);
	} else {
		SetMotorSpeed(-600);
	}

	while (IsGoalReached() == 0) {

	}

	SetMotorSpeed(0);
	goal_is_active = 0;
	GoalIsReached();
}

/**
  * @brief Return 1 if the goal is active (then the motor is still moving), or 0 if not (then the motor is still).
  */
int IsGoalActive() {
	return goal_is_active;
}

/**
  * @brief Move the motor backward until it trigger the 0 interrupt.
  */
void CheckForZero() {
	zero_is_found = 0;
	SetMotorSpeed(-600);
}

/**
  * @brief Return 1 if the Zero limit has been found, or 0 if not.
  */
int ZeroIsFound() {
	return zero_is_found;
}

/**
  * @brief Should be called when the 0 interrupt is triggered.
  */
void ZeroTriggered() {
	if (zero_is_found == 0) {
		SetMotorSpeed(0);
		encoder_0_value = GetCurrentPosition();
		zero_is_found = 1;
	}
}

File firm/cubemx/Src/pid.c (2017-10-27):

/* -----------------------------------------------------------------------------
 * pid
 * I-Grebot Dc motor PID library
 * -----------------------------------------------------------------------------
 * File        : pid.c
 * Language    : C
 * Author      : Sebastien Brulais
 * Creation    : 2013-06-07
 * -----------------------------------------------------------------------------
 * Library usage
 *
 *  /!\ Keep in mind that PID gains are sample time dependent
 *
 *  /!\ Do not forget to set a heap size in your linker for mallocs
 *  /!\ At least 4096 bytes /!\
 *
 * -----------------------------------------------------------------------------
 * Version     Comment                                   Author       Date
 * 1.0         Initial release                           Seb B.      2013-06-07
 * 1.1	       Separation speed/position update		     Pierrick B. 2013-12-11
 * 1.2         Adding PID Process + Testing              Pierrick B. 2014-01-04
 * -----------------------------------------------------------------------------
 */

#include "pid.h"
#include <stdlib.h>


int32_t PID_Process(PID_struct_t *PID, int32_t error)
{
    int32_t command;
    int32_t err_D;

    PID->last_err = PID->err;
    PID->err = error;
    PID->err_I += error;
    err_D = PID->last_err - PID->err;

    if(PID->KI!=0)
    {
        if(PID->err_I > PID->I_limit)
        {
            PID->err_I = PID->I_limit;
        }else if(PID->err_I < -PID->I_limit)
        {
            PID->err_I = -PID->I_limit;
        }
    }
    /*Main PID computation*/
    command = PID->err*PID->KP/100 + PID->err_I*PID->KI/1000 - err_D*PID->KD/100;

    return command;
 }

void PID_Process_Speed(PID_process_t *sPID, int32_t position){
    int32_t command=0;

    sPID->curr = (position - sPID->last);

    // Compute Speed errors
    command = PID_Process(sPID->PID, sPID->ref - sPID->curr);
   
    // Speed saturation
    if(sPID->speed_Limit)
    {
	if (command > sPID->speed_Limit)
	{
            command = sPID->speed_Limit;
        }else if (command < - sPID->speed_Limit)
	{
            command = - sPID->speed_Limit;
	}
    }

    // Acceleration saturation
    if(sPID->acceleration_Limit)
    {
        if ( (command - sPID->last_ref) > sPID->acceleration_Limit)
	{
            command = sPID->last_ref + sPID->acceleration_Limit;
	}else if (  (sPID->last_ref - command )  >  sPID->acceleration_Limit )
	{
            command = sPID->last_ref - sPID->acceleration_Limit;
	}
    }

    // Send new motor reference
    SetMotorSpeed(command);
    sPID->last_ref = command;
    sPID->last = position;
}

void PID_Process_Position(PID_process_t *pPID, PID_process_t *sPID, int32_t position){
    
    int32_t ref_speed;

    pPID->curr = position;
	
    // Compute position errors
    ref_speed = PID_Process(pPID->PID, pPID->ref - pPID->curr);
 
    // Speed saturation
    if(pPID->speed_Limit)
    {
	if (ref_speed > pPID->speed_Limit)
	{
            ref_speed = pPID->speed_Limit;
        }else if (ref_speed < - pPID->speed_Limit)
	{
            ref_speed = - pPID->speed_Limit;
	}
    }
	
    // Acceleration saturation
    if(pPID->acceleration_Limit)
    {
        if ( (ref_speed - pPID->last_ref) > pPID->acceleration_Limit)
	{
            ref_speed = pPID->last_ref + pPID->acceleration_Limit;
	}else if (  (pPID->last_ref - ref_speed )  >  pPID->acceleration_Limit )
	{
            ref_speed = pPID->last_ref - pPID->acceleration_Limit;
	}
    }

    
    if (sPID != NULL)
    {
        sPID->ref=ref_speed;
    	PID_Process_Speed(sPID,position);
    }
    else
    {
        // Send new motor reference
    	SetMotorSpeed(ref_speed);
        pPID->last_ref = ref_speed;
    }
}

void PID_Set_Coefficient(PID_struct_t *PID,int32_t KP,int32_t KI,int32_t KD,int32_t I_limit){
    // Set coefficients
    PID->KP = KP;
    PID->KI = KI;
    PID->KD = KD;
    PID->I_limit = I_limit;
}

void PID_Reset(PID_process_t *xPID){
    xPID->PID->I_limit = 0;
    xPID->PID->err = 0;
    xPID->PID->err_I = 0;
    xPID->PID->last_err = 0;
    xPID->last = 0;
    xPID->last_ref = 0;

    // Reset PID gains
    PID_Set_Coefficient(xPID->PID,0,0,0,0);
	
    PID_Set_limitation(xPID,0,0);
}

void PID_Set_limitation(PID_process_t *xPID,int32_t S_limit, int32_t A_limit){
    // Set Saturations
    xPID->speed_Limit = S_limit;
    xPID->acceleration_Limit = A_limit;
}

PID_process_t* pid_init(void){
    PID_process_t *xPID;
    xPID =(PID_process_t *) malloc(sizeof(PID_process_t));
    xPID->PID=(PID_struct_t *) malloc(sizeof(PID_struct_t));
    PID_Reset(xPID);
    return xPID;
}

void PID_Set_Cur_Position(PID_process_t *pPID, int32_t position) {
    pPID->curr = position;
}

void PID_Set_Ref_Position(PID_process_t *pPID, int32_t position) {
    pPID->ref = position;
}

int32_t PID_Get_Cur_Position(PID_process_t *pPID){
    return pPID->curr;
}

void PID_Set_Ref_Speed(PID_process_t *sPID, int16_t speed) {
    sPID->ref = speed;
}

int32_t PID_Get_Cur_Speed(PID_process_t *sPID){
    return sPID->curr;
}

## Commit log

2016-11-24 Added Eagle files
    [ServoIface_v1.0.brd, ServoIface_v1.0.sch]
2016-11-24 Adde dxf file for mecanichal purposes
    [ServoIface_v1.0.dxf]
2016-11-24 Added project's bill of material
    [ServoIface_v1.0_BOM.xlsx]
2016-12-16 Folder organizing, elec and firm
    [ServoIface_v1.0.brd, ServoIface_v1.0.dxf, ServoIface_v1.0.sch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]
2017-03-15 WIP: GPIO OK, ENCODER IN PROGRESS
2017-03-16 WIP: demo maker-faire without encoder
2017-03-18 WIP: demo maker-faire without encoder j2
2017-04-02 Encoders ok
2017-05-21 JST pas de capture event
2017-10-26 Adde PID library, not tested
2017-10-27 feature PID validated

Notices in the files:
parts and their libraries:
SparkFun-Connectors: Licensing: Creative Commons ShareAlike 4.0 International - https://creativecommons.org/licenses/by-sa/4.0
